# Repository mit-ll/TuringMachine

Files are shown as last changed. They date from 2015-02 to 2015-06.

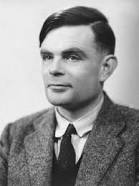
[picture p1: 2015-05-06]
student_code/Trevon/turing.jpg

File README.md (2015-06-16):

# A Turing Machine by MIT Lincoln Laboratory and the Community Charter School of Cambridge

During the spring semester in 2015, a team of MIT Lincoln Laboratory (http://www.ll.mit.edu/) staff volunteered there time to build a Turing machine with two high school seniors from the Community Charter School of Cambridge (http://www.ccscambridge.org/). This project helped the two seniors satisfy their internship requirement. The Turing machine was conceptualized by Alan Turing in 1936, but has been implemented in a more modern form.  The design uses 35mm film as memory, on which bits are physically written, read, and erased with a marker, camera, and mechanical eraser respectively.  These mechanisms are used to control the evolution of a state machine; fulfilling Turing's requirements for arbitrary computation.  The machine is controlled by embedded micro controllers, numerous motors and sensors, and code that was developed with the students.  The entire design for the machine, as well as the manufacturing and assembly, was created throughout the internship. The technical team from Lincoln Laboratory consisted of Chad Spensky, Benjamin Nahill, Timothy Greer, Matthew Harger, Stuart Baker, and Jack Lepird.  

## Contents
This repository contains all of the models, code, and bill of materials used to create our turing machine.

## Resources
  - [A Turing Machine](http://aturingmachine.com/)
  - [Turing Machine Emulator](http://www.turing.org.uk/turing/scrapbook/tmjava.html)
  - [Dimensions of 35mm film](http://www.brianpritchard.com/Fig%202.jpg)
  - [Dimensions of 35mm film (alt)](https://www.stereoscopy.com/faq/standard35ansi.gif)
  - [Robotic Calligraphy](http://calligraphybyherald.wix.com/herald#!gallery/c1zy6)

### Parts
 - [35mm Film Leader](http://www.numbersfilmsupply.com/categories/FILM-SUPPLIES/LEADER/)

## Raspberry Pi
 - [Touchscreen Drivers] (http://engineering-diy.blogspot.com/2013/01/adding-7inch-display-with-touchscreen.html)
 - [Modifying the Pi SD card on a Mac](http://pi.gbaman.info/?p=328)

### Setting up the console cable
 - The following [tutorial](https://learn.adafruit.com/downloads/pdf/adafruits-raspberry-pi-lesson-5-using-a-console-cable.pdf) worked perfectly.  Screen should be able connect to the serial port after you install the driver.

 >screen /dev/tty.usbserial 115200

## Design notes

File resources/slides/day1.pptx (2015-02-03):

## Cambridge Charter School Internship Building a Turing Machine

Chad Spensky, Tim Greer, Jack Lepird, Stuart Baker
Feb 3 2015

## Who are we?

- Chad Spensky
  - Area of Expertise: Computer Security
  - Education:
    - Bachelor’s Degree
      - Mathematics / Comp Sci. / Econ. @ PITT
    - Master’s Degree
      - Computer Security @ UNC-CH
  - Research Interests:
    - Authentication, Low-level Malware Analysis, Embedded Systems
  - Hobbies:
    - Snowboarding, Volleyball, Basketball, Inner Tube Water Polo, Traveling, Tinkering

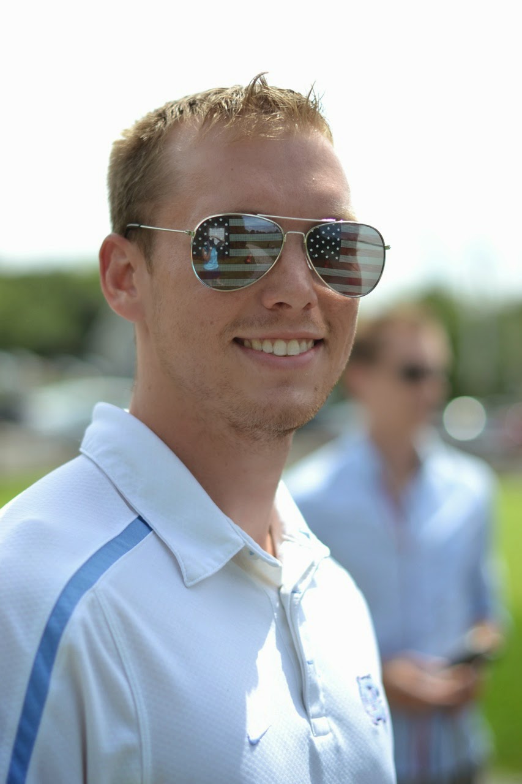
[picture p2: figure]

## Who are we?

- Jack Lepird
  - Areas of Expertise:
    - Machine Learning, Optimization, and Artificial Intelligence
  - Education:
    - Bachelor's Degree:
      - Mathematics / Operations Research / German, United States Air Force Academy
    - Master’s Degree (underway):
      - Operations Research, Massachusetts Institute of Technology
  - Research Interest:
    - Next-Generation Aircraft Collision Avoidance Systems
  - Hobbies:
    - Travel, SCUBA, Golf

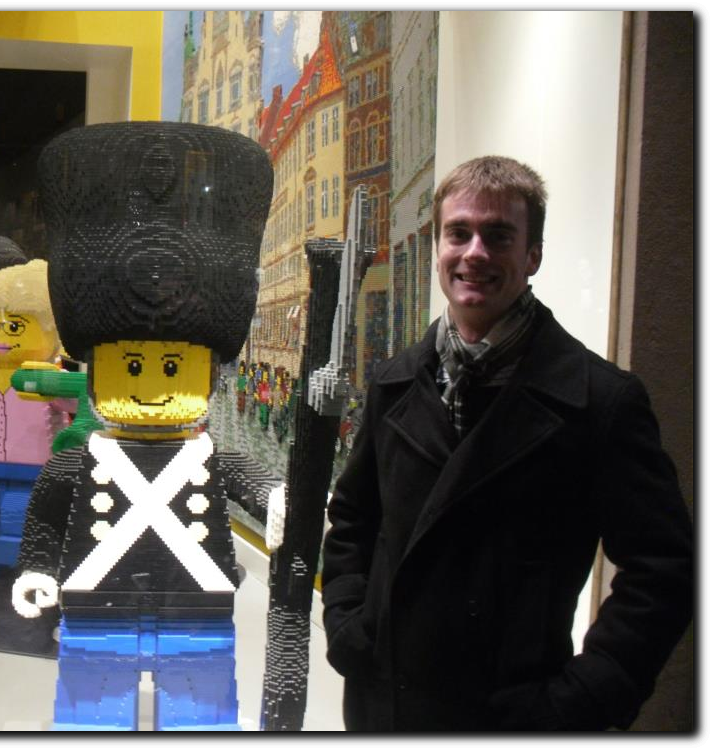
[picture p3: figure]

## Who are we?

- Tim Greer

## Who are we?

- Stuart Baker

## Who are you?

- What are your favorite subjects?
- What is your favorite food/color/animal?
- What do you do for fun?
- What do you hope to get out of this internship?

## Why are we here?

To Build a Turing Machine!

## Why are we here?

A WHAT?! Machine?

## Alan Turing

- One of the fathers of Computer Science
- Cracked German “Enigma” code during WWII
  - Shorted war by “two to four years”
- Solved “Entscheidungsproblem”
  - One of the “problems of the [20th] century”
- Could run marathon in under 2hrs 30 min
  - 5:45 minute miles
- Basically, a huge stud

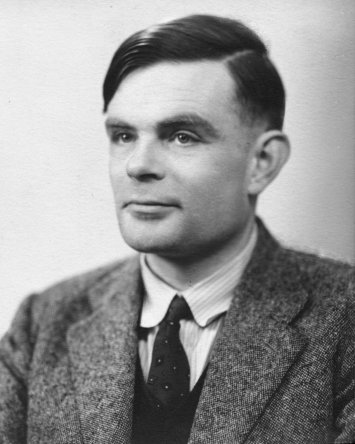
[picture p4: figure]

## What is a Turing Machine?

- A mental exercise
- Consists of three parts:
  - Tape
  - Head
  - “Machine State”
- Three operations:
  - Change symbol on tape
  - Move Tape
  - Change “state”

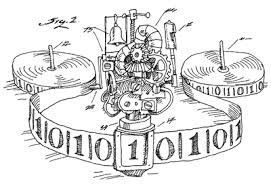
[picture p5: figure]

## So, why do we care?

- Anything computable can be run on a Turing Machine
  - Weird, right?
  - Weirder: In theory, the Turing machine is more powerful than your computer!
  - Studying a Turing machine can show us the limits of computing
- Provides a useful model for a Central Processing Unit (CPU) in an electronic computer

In fact, CPU instructions (right) look very similar to Turing Machine instructions

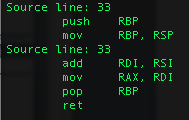
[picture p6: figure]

## Our semester goal

www.aturingmachine.com

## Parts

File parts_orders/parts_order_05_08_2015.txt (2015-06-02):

1 - 3ft of 6061 Aluminum (8mm Diameter) http://www.mcmaster.com/#standard-aluminum-rods/=x39eac
4 - Metric 18-8 Stainless Steel Unthreaded Spacer (4.5mm OD, 3mm Length, M3
Screw Size) http://www.mcmaster.com/#unthreaded-spacers/=x39gic

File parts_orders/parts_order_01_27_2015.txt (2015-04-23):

3 - Pi Starter Kits (https://www.adafruit.com/products/2125)
3 - Pi Cameras (https://www.adafruit.com/products/1367)
1 - Shift Registers (https://www.adafruit.com/products/450)
3 - Motor Kits (https://www.adafruit.com/products/1438)
3 - Motor Sheilds for Pi (https://www.adafruit.com/products/2348)
3 - Stepper Motors (https://www.adafruit.com/products/324)

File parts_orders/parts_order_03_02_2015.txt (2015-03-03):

1 - 35mm Film Leader/ Blue (http://www.ebay.com/itm/35MM-MOTION-PICTURE-FILM-LEADER-1000FT-ROLL-/351289908925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)
1 - Dry Erase Markers (http://www.amazon.com/Dry-Erase-Chalk-Marker-White/dp/B00L8BAXR0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)

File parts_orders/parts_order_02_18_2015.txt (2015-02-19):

2 - Power Supply for Monitor (http://www.amazon.com/Tontec%C2%AE-Supply-Adapter-Raspberry-Resolution/dp/B00LFBPL7K)
1 - Micro USB Cables (http://www.amazon.com/Anker-Premium-Android-Samsung-Motorola/dp/B00N8VHW72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)
5 - USB A to B (http://www.amazon.com/Belkin-3FT-USB-Device-Cable/dp/B00004Z5IU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)
1 - OpeanBeam (http://www.adafruit.com/products/1274)
3 - Motor Shields (http://www.adafruit.com/products/1438)
4 - Servos (http://www.adafruit.com/products/155)

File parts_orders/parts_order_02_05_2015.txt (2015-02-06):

2 - Touch Screen (http://www.amazon.com/Tontec-Raspberry-Display-AT070TN90-Touchscreen/dp/B00HNLXZHO)
3 - Raspberry Pi 2.0 (http://www.adafruit.com/products/2358)
3 - Multimeters (http://www.adafruit.com/products/2034)
3 - Keyboard/Mouse for Raspbery Pis (http://www.adafruit.com/products/1738)
2 - Film Leader/Our Tape (http://www.ebay.com/itm/Super-8mm-Film-Leader-50-ft-White-Leader-for-Super-8mm-/191495457883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)

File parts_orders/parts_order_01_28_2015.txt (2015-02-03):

3 - Pi Starter Kits (https://www.adafruit.com/products/2125)
3 - Pi Cameras (https://www.adafruit.com/products/1367)
1 - Shift Registers (https://www.adafruit.com/products/450)
3 - Motor Kits (https://www.adafruit.com/products/1438) [SOLD OUT]
3 - Motor Sheilds for Pi (https://www.adafruit.com/products/2348)
3 - Stepper Motors (https://www.adafruit.com/products/324)
3 - DC Motors (http://www.adafruit.com/products/711)
3 - Stepper Motors (http://www.adafruit.com/products/858)
3 - Solenoids (http://www.adafruit.com/products/412)
1 - Robotic Arm (http://www.adafruit.com/products/2012)
3 - Motor Kits (http://www.adafruit.com/products/1940)

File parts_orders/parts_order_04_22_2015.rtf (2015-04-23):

Things to Cut

Spools
4 - Laser cut spool holder sides
2 - Water jet base

Main Assembly
2 - Water jet base
1 - Main base
1 - Arm (top) for eraser
1 - Arm (bottom) for eraser
1 - Rail for marker arm (120mm)

Things to 3d Print

Spools
2 - Spool holder Hub
2 - Spool feeders with teeth for 35mm Film
2 - Spool timing pull (large)

Main Assembly
2 - Clamps for makers

Things to Buy

Overall
8mm Rod - http://www.banggood.com/OD-8mm-x-400mm-Bearing-Steel-Cylinder-Liner-Shaft-Optical-Axis-p-909003.html
2 Sheets of plastic (Black acrylic) - http://www.mcmaster.com/#8505k15/=wvbhm8

Spools
2 10K Potentiometer - https://www.adafruit.com/products/562
20 M3x10 tapered screws - http://www.metricscrews.us/index.php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
2 Stepper Brackets - https://solarbotics.com/product/52655/
2 Timing Pullys (Small) - https://sdp-si.com/eStore/Catalog/PartNumber/A%206Z%203-14DF03710
20 M3x30 Screws - hhttp://www.metricscrews.us/index.php?main_page=product_info&cPath=98_7_257&products_id=637 (https://www.etsy.com/listing/184820141/m3-x-30-mm-metric-machine-screws?kpid=184820141)

Main Assembly
1 Stepper Bracket - https://solarbotics.com/product/52655/
3 Servo Brackets - https://solarbotics.com/product/52650/
4 Bearing Mounts - https://solarbotics.com/product/52665/
3 Timing Pullys - https://sdp-si.com/eStore/Catalog/PartNumber/A%206Z%203-14DF03710

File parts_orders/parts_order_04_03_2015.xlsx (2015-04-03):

Part | Manufacturer | Manf # | Distributor | Dist # | Unit $ | Units | Total $ | Link
Aluminum plate, .125" Thick, 2 ft x 4 ft |  |  | McMaster Carr | 89015K28 | $50.58 | 1 | $50.58 | http://www.mcmaster.com/#89015k28/=wji07g
Multipurpose 6061 Aluminum Tube, 1 [ft] |  |  | McMaster Carr | 9056K74 | $9.18 | 1 | $9.18 | http://www.mcmaster.com/#9056k74/=wb0jrw
Architectural, 9/16" OD, 0.118" Wall, 2 [ft] |  |  | McMaster Carr | 1658T34 | $4.61 | 1 | $4.61 | http://www.mcmaster.com/#1658t34/=wjhpzd
Spacers, 6mm OD, 25mm Length, M3 |  |  | McMaster Carr | 94669A739 | $1.32 | 12 | $15.84 | http://www.mcmaster.com/#94669a739/=wde7l8
Clamp-on Shaft Collar, 8mm |  |  | McMaster Carr | 9506T4 | $4.14 | 4 | $16.56 | http://www.mcmaster.com/#9506t4/=wjhrlv
Aluminum Flat Washer, M8, 10 pack |  |  | McMaster Carr | 92334A116 | $10.22 | 1 | $10.22 | http://www.mcmaster.com/#92334a116/=wjhs23
Stepper Motor, NEMA 17 Frame |  | SM-42BYG011-25 | Sparfun | ROB-09238 | $14.95 | 3 | $44.85 | https://www.sparkfun.com/products/9238
Linear Stepper Motor |  | 39BYGL | Sparfun | ROB-10848 | $29.95 | 1 | $29.95 | https://www.sparkfun.com/products/10848
Low Profile Servo | Hitec | HS-77BB | Amazon | B0006O3WQY | $24.96 | 1 | $24.96 | http://www.amazon.com/Hitec-RCD-31077S-HS-77BB-Profile/dp/B0006O3WQY/
Shaft Support |  |  | Adafruit | 1182 | $3.95 | 4 | $15.80 | https://www.adafruit.com/products/1182
Aluminum Flex Shaft Coupler - 5mm to 8mm |  |  | Adafruit | 1176 | $4.95 | 3 | $14.85 | https://www.adafruit.com/products/1176
Radial Ball Bearing 608ZZ - Set of 4 |  |  | Adafruit | 1178 | $6.95 | 3 | $20.85 | https://www.adafruit.com/products/1252
Supported Slide Rail - 15mm wide - 500mm long |  |  | Adafruit | 1861 | $29.95 | 1 | $29.95 | https://www.adafruit.com/products/1861
15mm Slide Railing Platform - Smaller Size |  |  | Adafruit | 1860 | $21.95 | 1 | $21.95 | https://www.adafruit.com/products/1860
Timing Pulley, XL Pitch, 14 Teeth |  |  | SDP-SI | A 6Z 3-14DF03710 | $7.42 | 5 | $37.10 | https://sdp-si.com/eStore/Catalog/PartNumber/A%206Z%203-14DF03710
UV Leds |  |  | Adafruit | 1793 | $4.95 | 1 | $4.95 | http://www.adafruit.com/products/1793
Camera Ribbon Cable |  |  | Adafruit | 1731 | $2.95 | 1 | $2.95 | http://www.adafruit.com/products/1731
Dry Erase Makers (Neon) |  |  | Amazon | SAN1752226 | $6.70 | 1 | $6.70 | http://www.amazon.com/Expo-Bullet-Erase-Markers-Colored/dp/B0033AGVVG
Dry Erase Markers (Glow) |  |  | Amazon | 79551 | $8.99 | 1 | $8.99 | http://www.amazon.com/Quartet-Glo-write-Dry-Erase-Assorted-79551/dp/B008DQXN48
 |  |  |  |  |  | Total | $370.84

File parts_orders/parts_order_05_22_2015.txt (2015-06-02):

1 - http://www.mcmaster.com/#6484k231/=xa42p9
1 - http://www.mcmaster.com/#6484k23/=xa43nw
1 - http://www.mcmaster.com/#6484k232/=xa43of
2 - http://www.mcmaster.com/#6484K228

2 - http://www.mcmaster.com/#6484k227/=xalcii

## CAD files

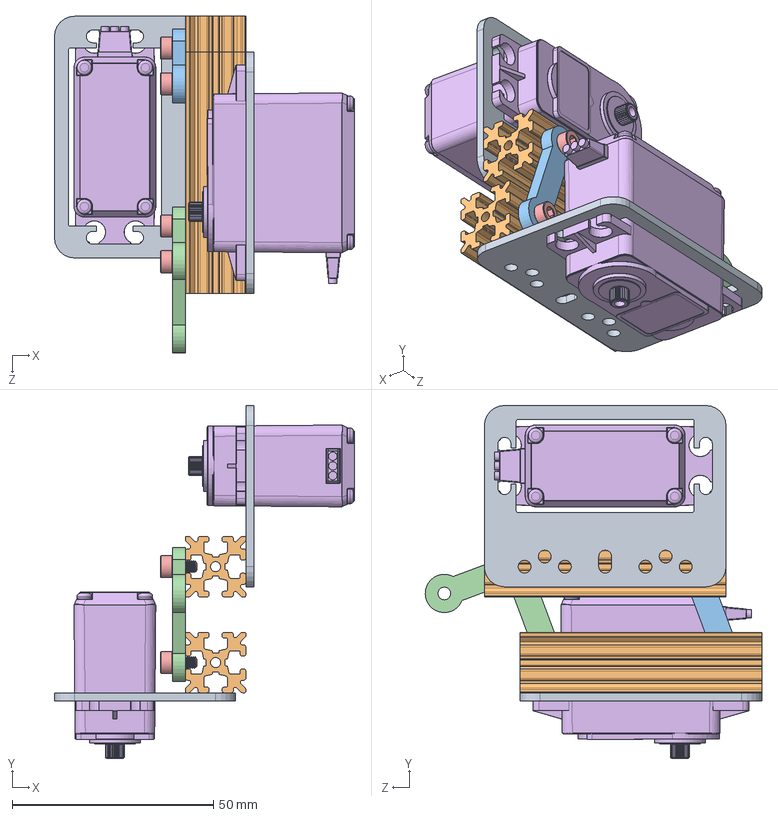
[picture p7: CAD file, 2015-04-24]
models/Gantry/Eraser/Assemembly_Eraser.SLDASM
74.5 x 87.6 x 83.5 mm
Plate_Servo_Mount x 2
Eraser_Beam_Riser x 2
Lift_Arm
Lift_Arm_Driven
Bolt_M3_6mm x 4
Servo x 2

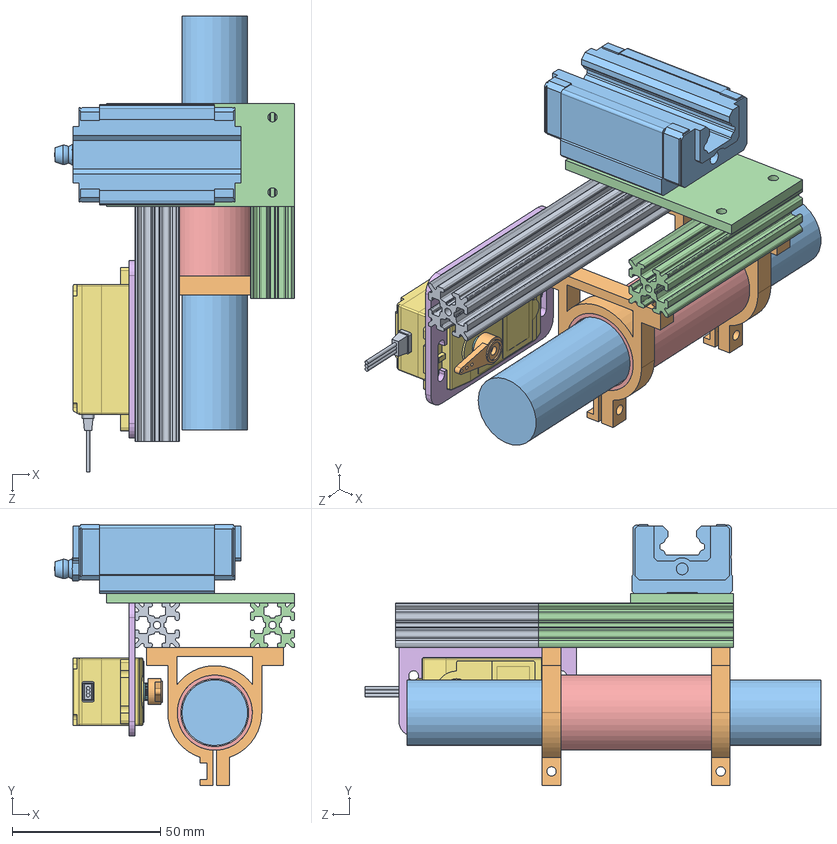
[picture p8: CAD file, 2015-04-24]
models/Gantry/Marker_Holder/Assembly_Marker_Holder.SLDASM
81.2 x 88.1 x 153.9 mm
Beam_Clamp_Riser
gantry_marker_clamp x 2
whiteboad_marker
Beam_Clamp_Riser_Short
Marker_Tube
Plate_Servo_Mount
Servo_SDS-S0070_Body
Servo_SDS-S0070_Shaft
Servo_SDS-S0070_Connector
Servo_SDS-S0070_Horn
Adafruit_Guide_Carriage
Carriage_Mounting_Plate

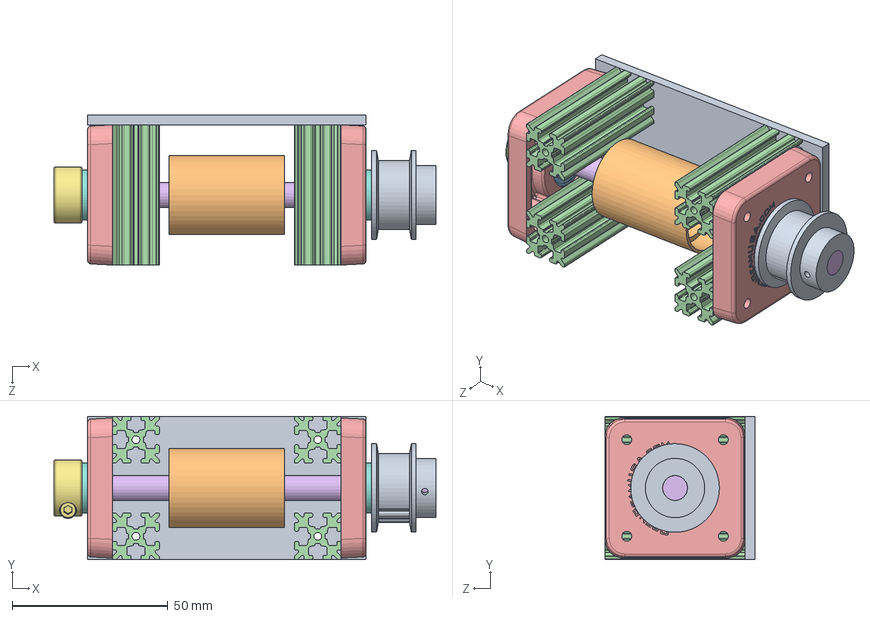
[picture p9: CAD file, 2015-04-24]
models/Gantry/Film_Feeder/Assembly_Film_Feeder.SLDASM
122.6 x 46.0 x 48.2 mm
Base_Plate
Film_Sprocket
Bearing_ID6mm_OD22mm x 2
Beam_Riser x 4
Plate_608_to_NEMA17 x 2
Feeder_Support_Rod
Shaft_Collar
Washer_M8 x 2
Timing_Pulley_14T

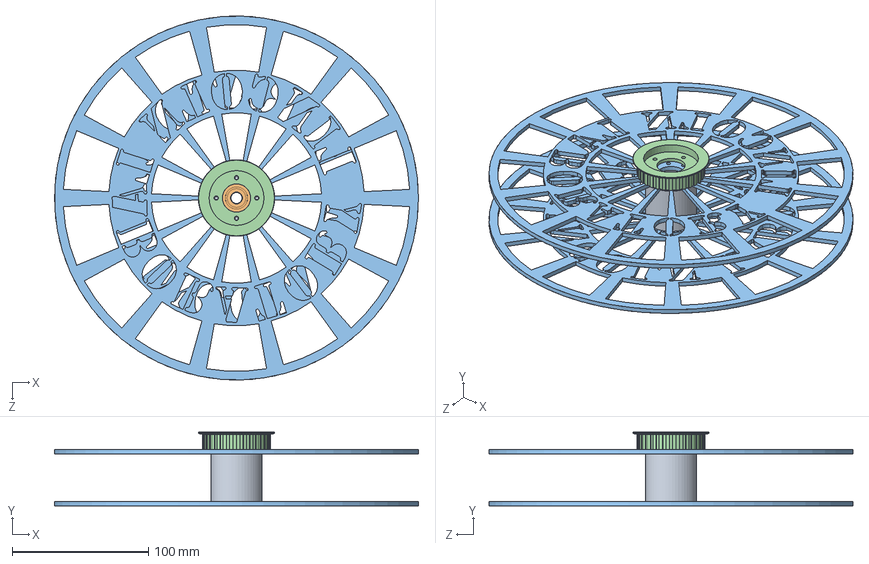
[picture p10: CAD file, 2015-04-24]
models/Spool_Holder/Spool/Assembly_Spool.SLDASM
266.7 x 54.1 x 266.6 mm
Spool_Hub
Bearing_ID6mm_OD22mm x 2
Spool_Side_Plate x 2
Timing_Pulley

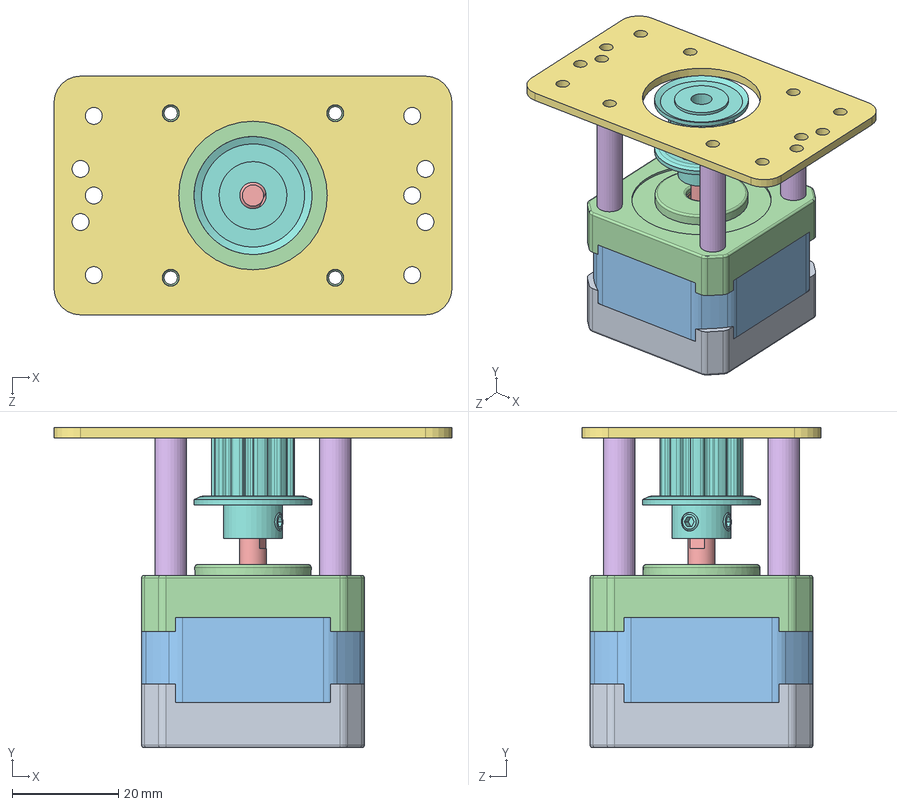
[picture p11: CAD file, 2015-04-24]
models/Gantry/Assembly_Film_Drive.SLDASM
75.0 x 60.4 x 45.0 mm
NEMA17_Bottom_33mm
radial ball bearing_68_din x 2
NEMA17_Middle_33mm
NEMA17_Top_33mm
NEMA17_Shaft_33mm
Motor_Spacer x 4
Plate_NEMA_17
Timing_Belt_Gear_11T

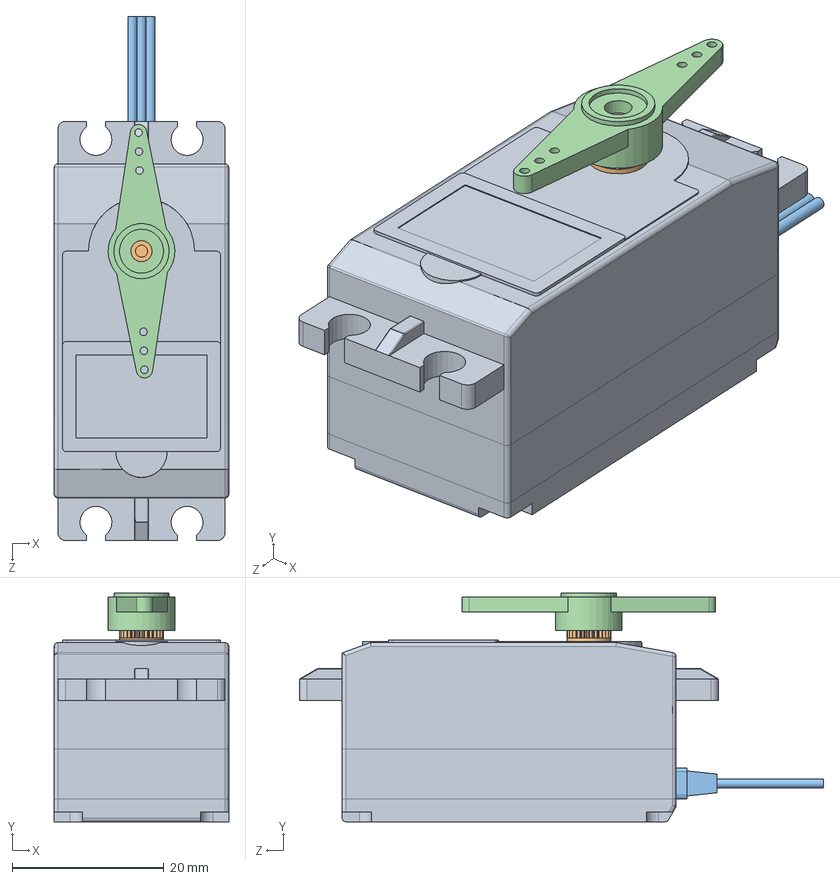
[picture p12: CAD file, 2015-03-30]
models/Gantry/Marker_Holder/Servo/Assembly_Servo_SDS-S0070.SLDASM
23.0 x 30.1 x 69.0 mm
Servo_SDS-S0070_Body
Servo_SDS-S0070_Shaft
Servo_SDS-S0070_Connector
Servo_SDS-S0070_Horn

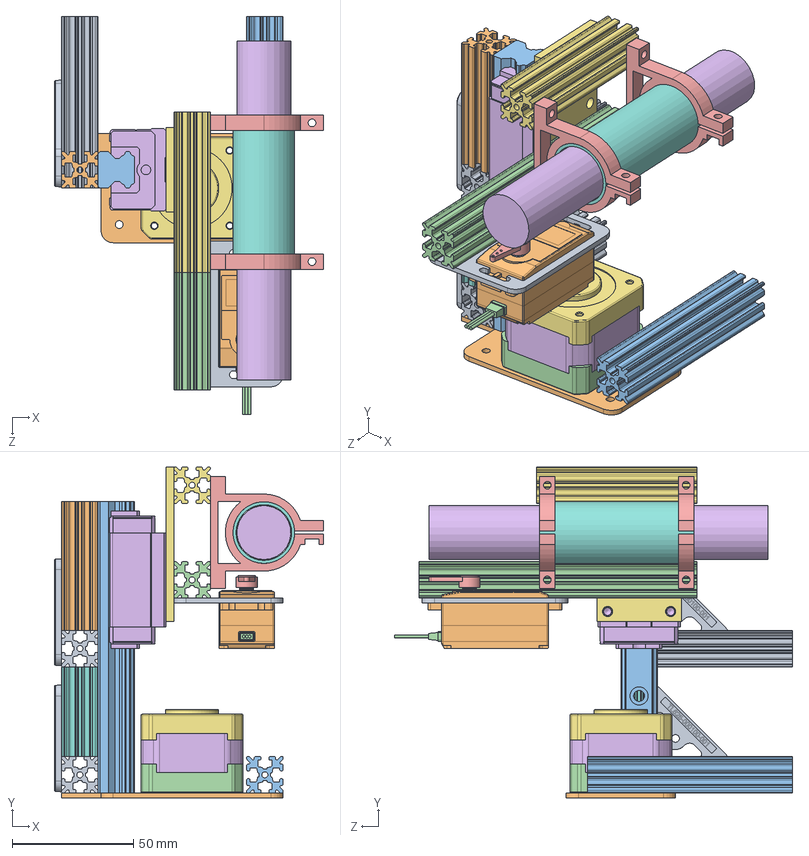
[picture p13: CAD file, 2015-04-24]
models/Gantry/Assembly_Gantry_Superstructure.SLDASM
110.8 x 136.3 x 163.9 mm
Beam_Gantry_Riser x 2
Beam_Gantry_Runner
Adafruit_Guide_Rail_Cut
Beam_Clamp_Riser
gantry_marker_clamp x 2
whiteboad_marker
Beam_Clamp_Riser_Short
Marker_Tube
Plate_Servo_Mount
Servo_SDS-S0070_Body
Servo_SDS-S0070_Shaft
Servo_SDS-S0070_Connector
Servo_SDS-S0070_Horn
Adafruit_Guide_Carriage
Carriage_Mounting_Plate
Beam_Gantry_Runner_Short
Plate_L x 2
Plate_NEMA_Modified
Beam_Gantry_Riser_Tall
NEMA17_Bottom_33mm
radial ball bearing_68_din x 2
NEMA17_Middle_33mm
NEMA17_Top_33mm

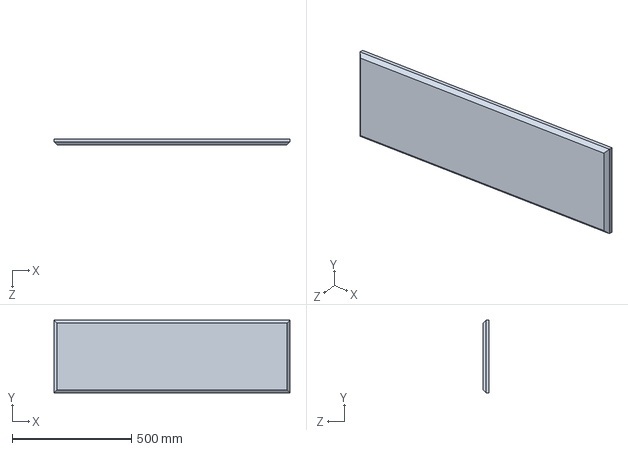
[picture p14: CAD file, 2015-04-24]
models/Display_Base.SLDPRT
990.6 x 304.8 x 25.4 mm

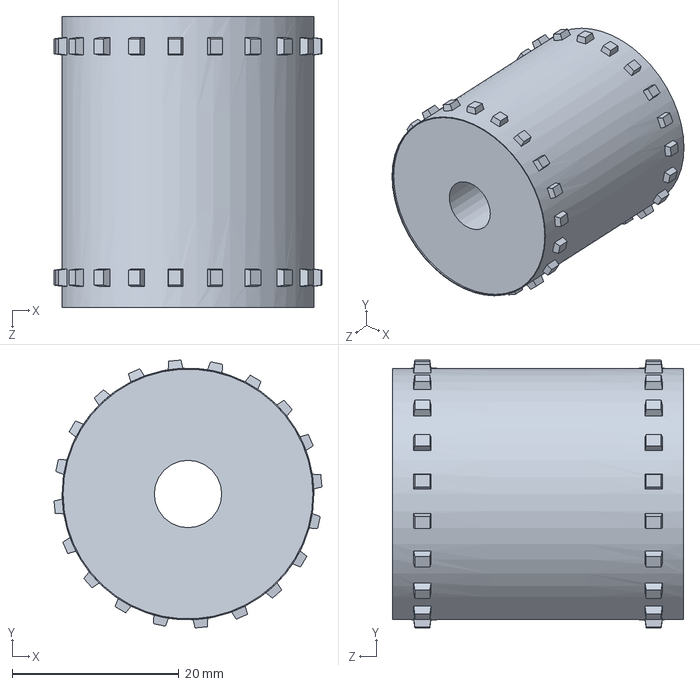
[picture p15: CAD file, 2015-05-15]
models/Gantry/Film_Feeder/Film_Sprocket.SLDPRT
32.2 x 32.2 x 35.0 mm

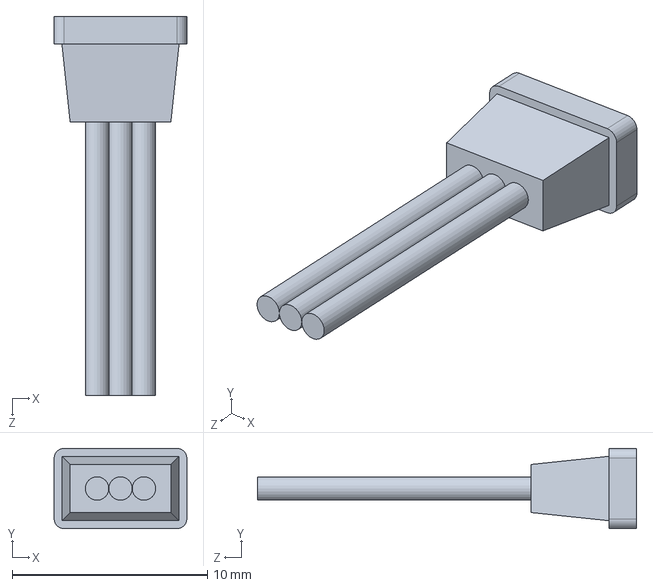
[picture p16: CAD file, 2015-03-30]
models/Gantry/Marker_Holder/Servo/Servo_SDS-S0070_Connector.SLDPRT
6.80 x 4.10 x 19.4 mm

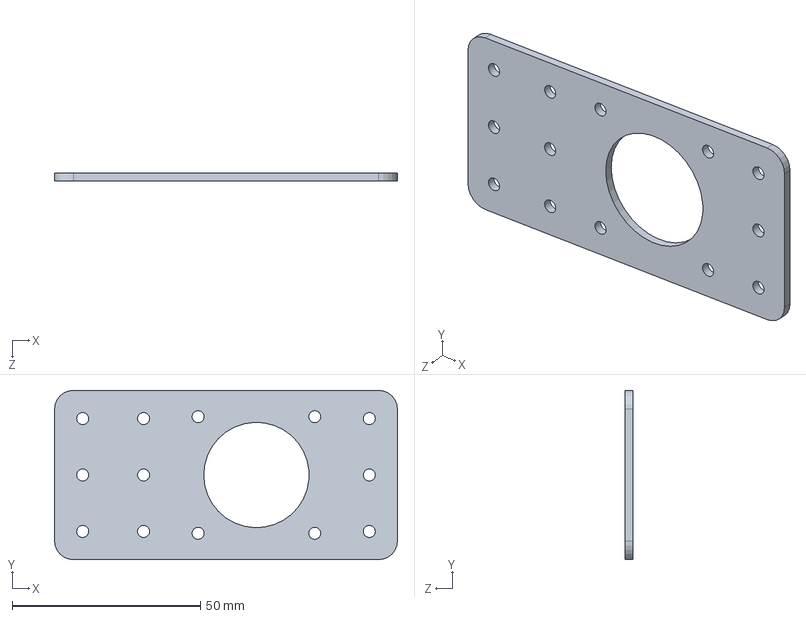
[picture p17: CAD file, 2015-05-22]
models/Gantry/Plate_NEMA_Modified2.SLDPRT
91.2 x 45.0 x 2.03 mm

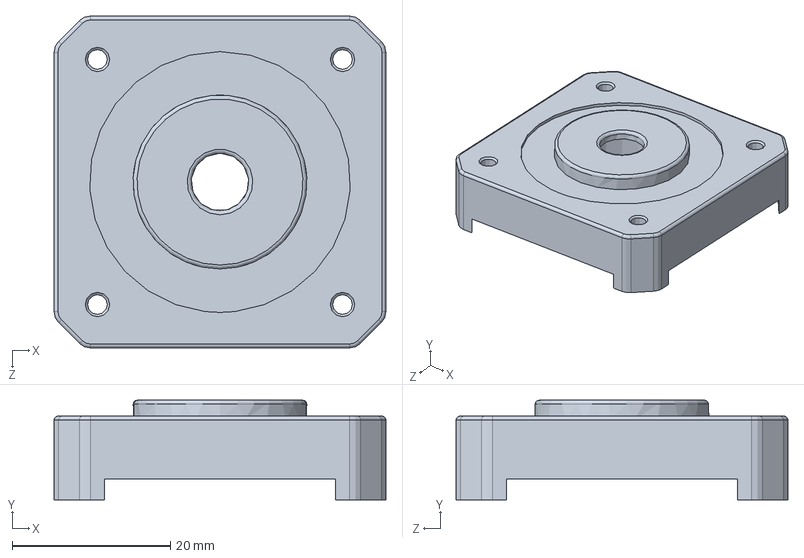
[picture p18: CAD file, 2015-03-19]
models/Nema-17_33mm/NEMA17_Top_33mm.SLDPRT
42.0 x 12.6 x 42.0 mm

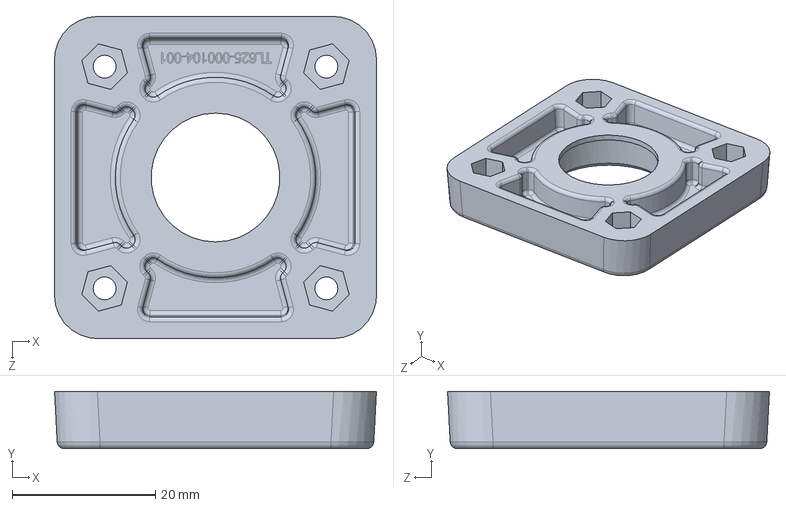
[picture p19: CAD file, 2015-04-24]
models/OpenBeam/Bearing_to_NEMA17/TL625-000104-001_-_608_to_NEMA_17_Adapter.SLDPRT
45.0 x 8.00 x 45.0 mm

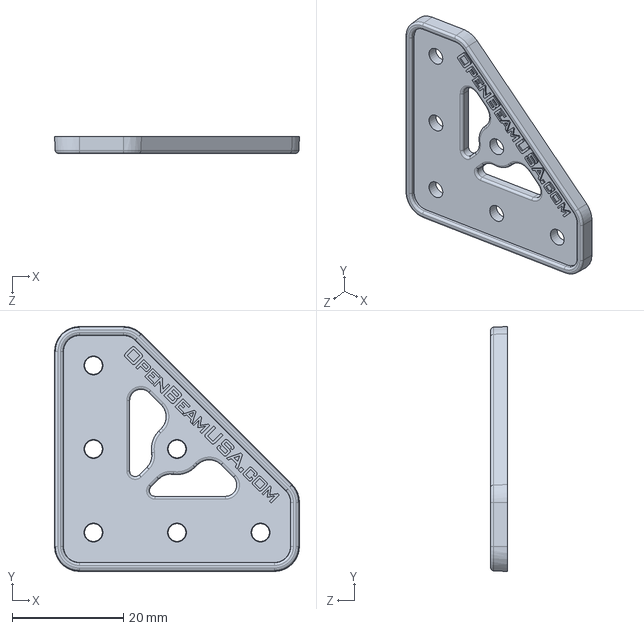
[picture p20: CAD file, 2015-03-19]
models/OpenBeam/L_Bracket/TL625-000100-002_-_L_Plate_OpenBeam_1515.SLDPRT
44.0 x 44.0 x 3.00 mm

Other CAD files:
models/OpenBeam/Motor_Mount_NEMA17/TL400-000105-002_-_NEMA_17_Motor_Mount.SLDPRT
models/OpenBeam/OpenBeam_Extrusion/TL-400-0101-002.SLDPRT
models/OpenBeam/Servo_Mount/TL400-000104-004_-_Plate_Servo_Mount_OpenBeam_1515.SLDPRT
models/OpenBeam/Shaft_Clamp/TL625-000102-001_-_SHAFT_CLAMP_OpenBeam_1515.SLDPRT
models/Adafruit_Guide_Carriage.SLDPRT
models/Adafruit_Guide_Rail.SLDPRT
models/Adafruit_Guide_Rail_Cut.SLDPRT
models/Adafruit_Rod_Support.SLDPRT
models/Angle_Connector.SLDPRT
models/Bearing_ID6mm_OD22mm.SLDPRT
models/Bolt_M3_10mm.SLDPRT
models/Bolt_M3_6mm.SLDPRT
models/Bolt_M3_8mm.SLDPRT
models/Coupler_8mm_5mm.SLDPRT
models/Gantry/Beam_Carraige_Riser.SLDPRT
models/Gantry/Beam_Carraige_Runner.SLDPRT
models/Gantry/Beam_Gantry_Riser.SLDPRT
models/Gantry/Beam_Gantry_Riser_Tall.SLDPRT
models/Gantry/Beam_Gantry_Runner.SLDPRT
models/Gantry/Beam_Gantry_Runner_Short.SLDPRT
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

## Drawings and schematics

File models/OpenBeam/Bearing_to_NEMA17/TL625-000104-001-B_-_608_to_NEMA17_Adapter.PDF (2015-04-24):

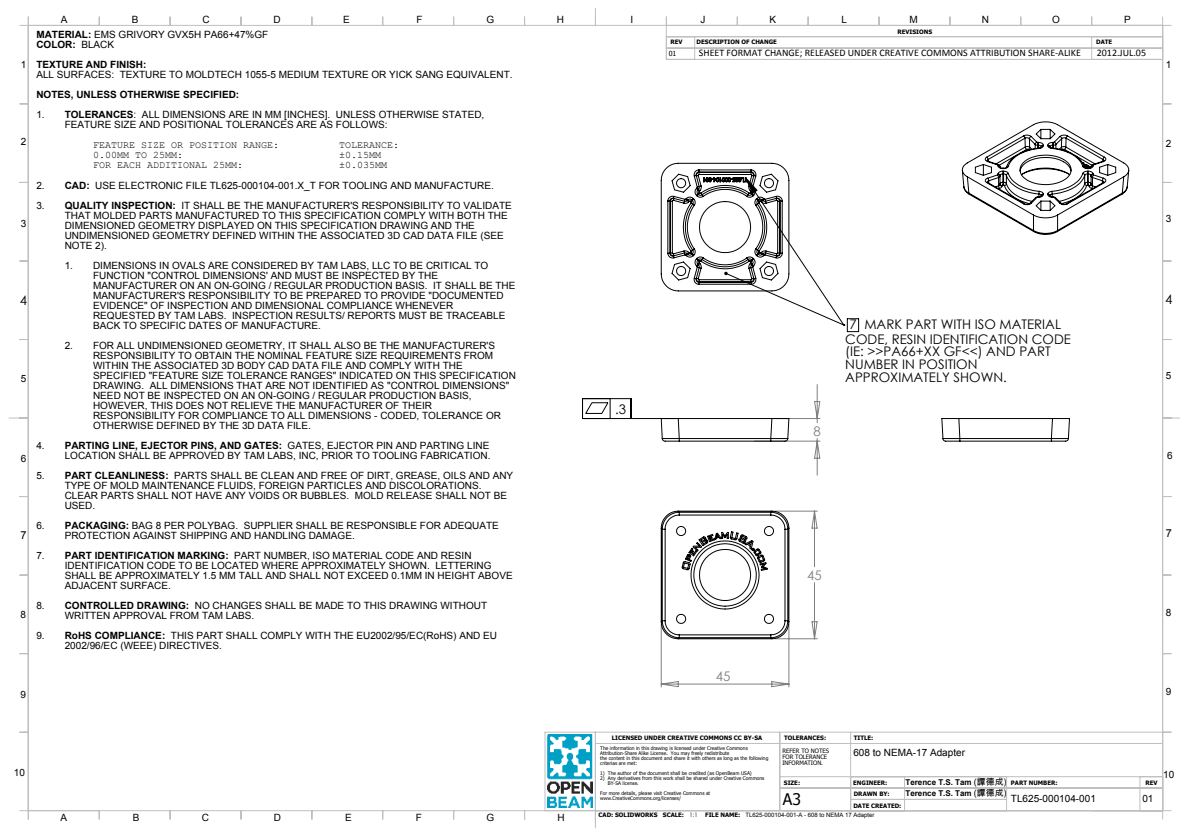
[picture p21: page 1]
FEATURE SIZE OR POSITION RANGE:; TOLERANCE:; FOR EACH ADDITIONAL 25MM:; CAD: SOLIDWORKS SCALE:; FILE NAME: 1:1; TL625-000104-001 DRAWN BY:; DATE CREATED:

MATERIAL: EMS GRIVORY GVX5H PA66+47%GF
COLOR: BLACK
TEXTURE AND FINISH:
ALL SURFACES: TEXTURE TO MOLDTECH 1055-5 MEDIUM TEXTURE OR YICK SANG EQUIVALENT.
NOTES, UNLESS OTHERWISE SPECIFIED:
1. TOLERANCES: ALL DIMENSIONS ARE IN MM [INCHES]. UNLESS OTHERWISE STATED,
FEATURE SIZE AND POSITIONAL TOLERANCES ARE AS FOLLOWS:

REV | DESCRIPTION OF CHANGE | DATE
01 | SHEET FORMAT CHANGE; RELEASED UNDER CREATIVE COMMONS ATTRIBUTION SHARE-ALIKE | 2012.JUL.05

2. CAD: USE ELECTRONIC FILE TL625-000104-001.X_T FOR TOOLING AND MANUFACTURE.
3. QUALITY INSPECTION: IT SHALL BE THE MANUFACTURER'S RESPONSIBILITY TO VALIDATE
THAT MOLDED PARTS MANUFACTURED TO THIS SPECIFICATION COMPLY WITH BOTH THE
DIMENSIONED GEOMETRY DISPLAYED ON THIS SPECIFICATION DRAWING AND THE
UNDIMENSIONED GEOMETRY DEFINED WITHIN THE ASSOCIATED 3D CAD DATA FILE (SEE
NOTE 2).
1. DIMENSIONS IN OVALS ARE CONSIDERED BY TAM LABS, LLC TO BE CRITICAL TO
FUNCTION "CONTROL DIMENSIONS' AND MUST BE INSPECTED BY THE
MANUFACTURER ON AN ON-GOING / REGULAR PRODUCTION BASIS. IT SHALL BE THE
MANUFACTURER'S RESPONSIBILITY TO BE PREPARED TO PROVIDE "DOCUMENTED
EVIDENCE" OF INSPECTION AND DIMENSIONAL COMPLIANCE WHENEVER
REQUESTED BY TAM LABS. INSPECTION RESULTS/ REPORTS MUST BE TRACEABLE
BACK TO SPECIFIC DATES OF MANUFACTURE.
2. FOR ALL UNDIMENSIONED GEOMETRY, IT SHALL ALSO BE THE MANUFACTURER'S
RESPONSIBILITY TO OBTAIN THE NOMINAL FEATURE SIZE REQUIREMENTS FROM
WITHIN THE ASSOCIATED 3D BODY CAD DATA FILE AND COMPLY WITH THE
SPECIFIED "FEATURE SIZE TOLERANCE RANGES" INDICATED ON THIS SPECIFICATION
DRAWING. ALL DIMENSIONS THAT ARE NOT IDENTIFIED AS "CONTROL DIMENSIONS"
NEED NOT BE INSPECTED ON AN ON-GOING / REGULAR PRODUCTION BASIS,
HOWEVER, THIS DOES NOT RELIEVE THE MANUFACTURER OF THEIR
RESPONSIBILITY FOR COMPLIANCE TO ALL DIMENSIONS - CODED, TOLERANCE OR
OTHERWISE DEFINED BY THE 3D DATA FILE.

7 MARK PART WITH ISO MATERIAL
CODE, RESIN IDENTIFICATION CODE
(IE: >>PA66+XX GF<<) AND PART
NUMBER IN POSITION
APPROXIMATELY SHOWN.

4. PARTING LINE, EJECTOR PINS, AND GATES: GATES, EJECTOR PIN AND PARTING LINE
LOCATION SHALL BE APPROVED BY TAM LABS, INC, PRIOR TO TOOLING FABRICATION.
5. PART CLEANLINESS: PARTS SHALL BE CLEAN AND FREE OF DIRT, GREASE, OILS AND ANY
TYPE OF MOLD MAINTENANCE FLUIDS, FOREIGN PARTICLES AND DISCOLORATIONS.
CLEAR PARTS SHALL NOT HAVE ANY VOIDS OR BUBBLES. MOLD RELEASE SHALL NOT BE
USED.
6. PACKAGING: BAG 8 PER POLYBAG. SUPPLIER SHALL BE RESPONSIBLE FOR ADEQUATE
7. PART IDENTIFICATION MARKING: PART NUMBER, ISO MATERIAL CODE AND RESIN
IDENTIFICATION CODE TO BE LOCATED WHERE APPROXIMATELY SHOWN. LETTERING
SHALL BE APPROXIMATELY 1.5 MM TALL AND SHALL NOT EXCEED 0.1MM IN HEIGHT ABOVE
ADJACENT SURFACE.
8. CONTROLLED DRAWING: NO CHANGES SHALL BE MADE TO THIS DRAWING WITHOUT
9. RoHS COMPLIANCE: THIS PART SHALL COMPLY WITH THE EU2002/95/EC(RoHS) AND EU
2002/96/EC (WEEE) DIRECTIVES.

PROTECTION AGAINST SHIPPING AND HANDLING DAMAGE.

WRITTEN APPROVAL FROM TAM LABS.

LICENSED UNDER CREATIVE COMMONS CC BY-SA

The information in this drawing is licensed under Creative Commons
Attribution-Share Alike License. You may freely redistribute
the content in this document and share it with others as long as the following
criterias are met:
1) The author of the document shall be credited (as OpenBeam USA)
2) Any derivatives from this work shall be shared under Creative Commons
BY-SA license.
For more details, please visit Creative Commons at
www.CreativeCommons.org/licenses/

REFER TO NOTES FOR TOLERANCE INFORMATION. | 608 to NEMA-17 Adapter

SIZE: | ENGINEER: | Terence T.S. Tam (譚德成) | PART NUMBER: | REV

Terence T.S. Tam (譚德成)

TL625-000104-001-A - 608 to NEMA 17 Adapter

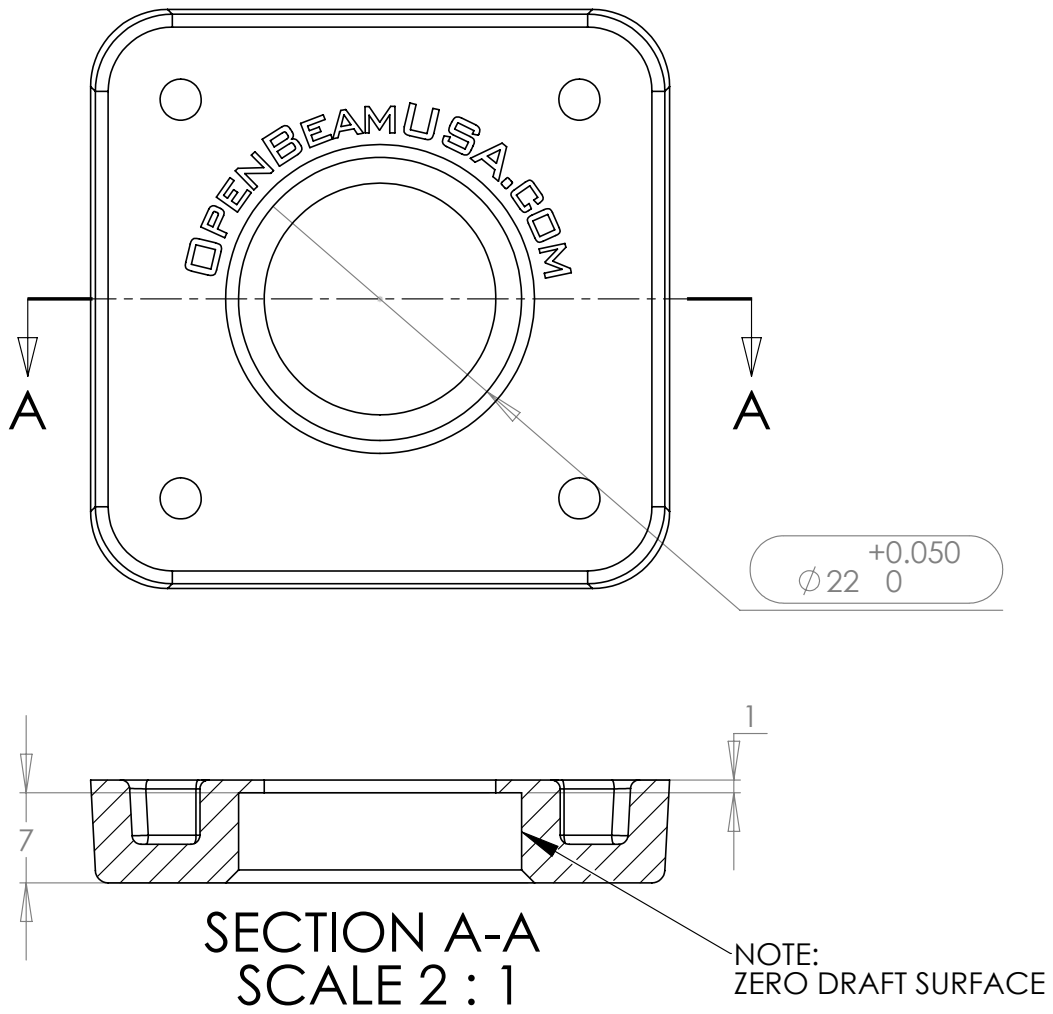
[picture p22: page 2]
SECTION A-A; SCALE 2 : 1; NOTE:; CAD: SOLIDWORKS SCALE:; FILE NAME: 1:1; TL625-000104-001 DRAWN BY:; DATE CREATED:

SEE REVISION BLOCK ON PAGE 1

ZERO DRAFT SURFACE

LICENSED UNDER CREATIVE COMMONS CC BY-SA

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

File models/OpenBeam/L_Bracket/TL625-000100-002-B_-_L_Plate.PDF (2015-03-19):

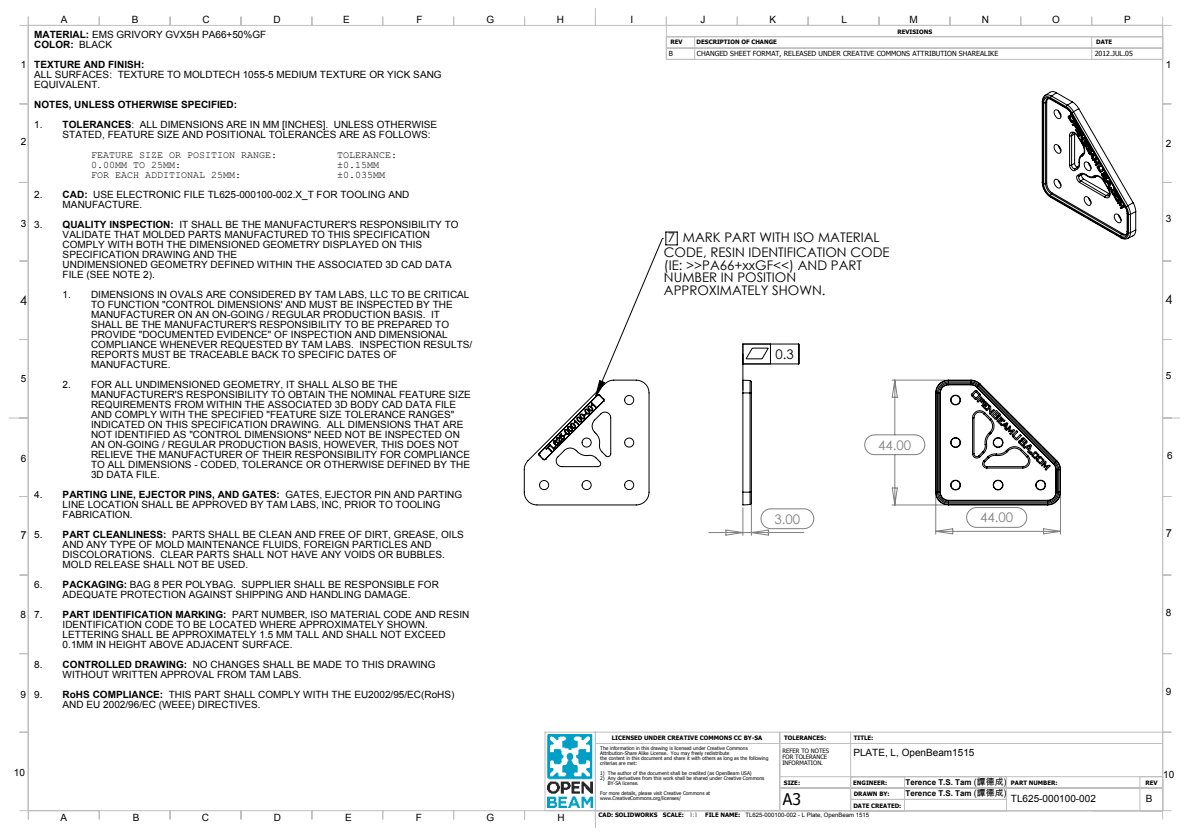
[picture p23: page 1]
FEATURE SIZE OR POSITION RANGE:; TOLERANCE:; FOR EACH ADDITIONAL 25MM:; CAD: SOLIDWORKS SCALE:; FILE NAME: 1:1; TL625-000100-002 DRAWN BY:; DATE CREATED: TL625-000100-002 - L Plate, OpenBeam 1515

MATERIAL: EMS GRIVORY GVX5H PA66+50%GF
COLOR: BLACK
TEXTURE AND FINISH:
ALL SURFACES: TEXTURE TO MOLDTECH 1055-5 MEDIUM TEXTURE OR YICK SANG
EQUIVALENT.
NOTES, UNLESS OTHERWISE SPECIFIED:
1. TOLERANCES: ALL DIMENSIONS ARE IN MM [INCHES]. UNLESS OTHERWISE
STATED, FEATURE SIZE AND POSITIONAL TOLERANCES ARE AS FOLLOWS:

REV | DESCRIPTION OF CHANGE | DATE
B | CHANGED SHEET FORMAT, RELEASED UNDER CREATIVE COMMONS ATTRIBUTION SHAREALIKE | 2012.JUL.05

2. CAD: USE ELECTRONIC FILE TL625-000100-002.X_T FOR TOOLING AND
MANUFACTURE.
3. QUALITY INSPECTION: IT SHALL BE THE MANUFACTURER'S RESPONSIBILITY TO
VALIDATE THAT MOLDED PARTS MANUFACTURED TO THIS SPECIFICATION
COMPLY WITH BOTH THE DIMENSIONED GEOMETRY DISPLAYED ON THIS
SPECIFICATION DRAWING AND THE
UNDIMENSIONED GEOMETRY DEFINED WITHIN THE ASSOCIATED 3D CAD DATA
FILE (SEE NOTE 2).
1. DIMENSIONS IN OVALS ARE CONSIDERED BY TAM LABS, LLC TO BE CRITICAL

7 MARK PART WITH ISO MATERIAL
CODE, RESIN IDENTIFICATION CODE
(IE: >>PA66+xxGF<<) AND PART
NUMBER IN POSITION
APPROXIMATELY SHOWN.

TO FUNCTION "CONTROL DIMENSIONS' AND MUST BE INSPECTED BY THE
MANUFACTURER ON AN ON-GOING / REGULAR PRODUCTION BASIS. IT
SHALL BE THE MANUFACTURER'S RESPONSIBILITY TO BE PREPARED TO
PROVIDE "DOCUMENTED EVIDENCE" OF INSPECTION AND DIMENSIONAL
COMPLIANCE WHENEVER REQUESTED BY TAM LABS. INSPECTION RESULTS/
REPORTS MUST BE TRACEABLE BACK TO SPECIFIC DATES OF
2. FOR ALL UNDIMENSIONED GEOMETRY, IT SHALL ALSO BE THE
MANUFACTURER'S RESPONSIBILITY TO OBTAIN THE NOMINAL FEATURE SIZE
REQUIREMENTS FROM WITHIN THE ASSOCIATED 3D BODY CAD DATA FILE
AND COMPLY WITH THE SPECIFIED "FEATURE SIZE TOLERANCE RANGES"
INDICATED ON THIS SPECIFICATION DRAWING. ALL DIMENSIONS THAT ARE
NOT IDENTIFIED AS "CONTROL DIMENSIONS" NEED NOT BE INSPECTED ON
AN ON-GOING / REGULAR PRODUCTION BASIS, HOWEVER, THIS DOES NOT
RELIEVE THE MANUFACTURER OF THEIR RESPONSIBILITY FOR COMPLIANCE
TO ALL DIMENSIONS - CODED, TOLERANCE OR OTHERWISE DEFINED BY THE
3D DATA FILE.

4. PARTING LINE, EJECTOR PINS, AND GATES: GATES, EJECTOR PIN AND PARTING
LINE LOCATION SHALL BE APPROVED BY TAM LABS, INC, PRIOR TO TOOLING
FABRICATION.
5. PART CLEANLINESS: PARTS SHALL BE CLEAN AND FREE OF DIRT, GREASE, OILS
AND ANY TYPE OF MOLD MAINTENANCE FLUIDS, FOREIGN PARTICLES AND
DISCOLORATIONS. CLEAR PARTS SHALL NOT HAVE ANY VOIDS OR BUBBLES.
MOLD RELEASE SHALL NOT BE USED.
6. PACKAGING: BAG 8 PER POLYBAG. SUPPLIER SHALL BE RESPONSIBLE FOR
ADEQUATE PROTECTION AGAINST SHIPPING AND HANDLING DAMAGE.
7. PART IDENTIFICATION MARKING: PART NUMBER, ISO MATERIAL CODE AND RESIN
IDENTIFICATION CODE TO BE LOCATED WHERE APPROXIMATELY SHOWN.
LETTERING SHALL BE APPROXIMATELY 1.5 MM TALL AND SHALL NOT EXCEED
0.1MM IN HEIGHT ABOVE ADJACENT SURFACE.
8. CONTROLLED DRAWING: NO CHANGES SHALL BE MADE TO THIS DRAWING
WITHOUT WRITTEN APPROVAL FROM TAM LABS.
9. RoHS COMPLIANCE: THIS PART SHALL COMPLY WITH THE EU2002/95/EC(RoHS)
AND EU 2002/96/EC (WEEE) DIRECTIVES.

LICENSED UNDER CREATIVE COMMONS CC BY-SA

The information in this drawing is licensed under Creative Commons
Attribution-Share Alike License. You may freely redistribute
the content in this document and share it with others as long as the following
criterias are met:
1) The author of the document shall be credited (as OpenBeam USA)
2) Any derivatives from this work shall be shared under Creative Commons
BY-SA license.
For more details, please visit Creative Commons at
www.CreativeCommons.org/licenses/

REFER TO NOTES FOR TOLERANCE INFORMATION. | PLATE, L, OpenBeam1515

SIZE: | ENGINEER: | Terence T.S. Tam (譚德成) | PART NUMBER: | REV

Terence T.S. Tam (譚德成)

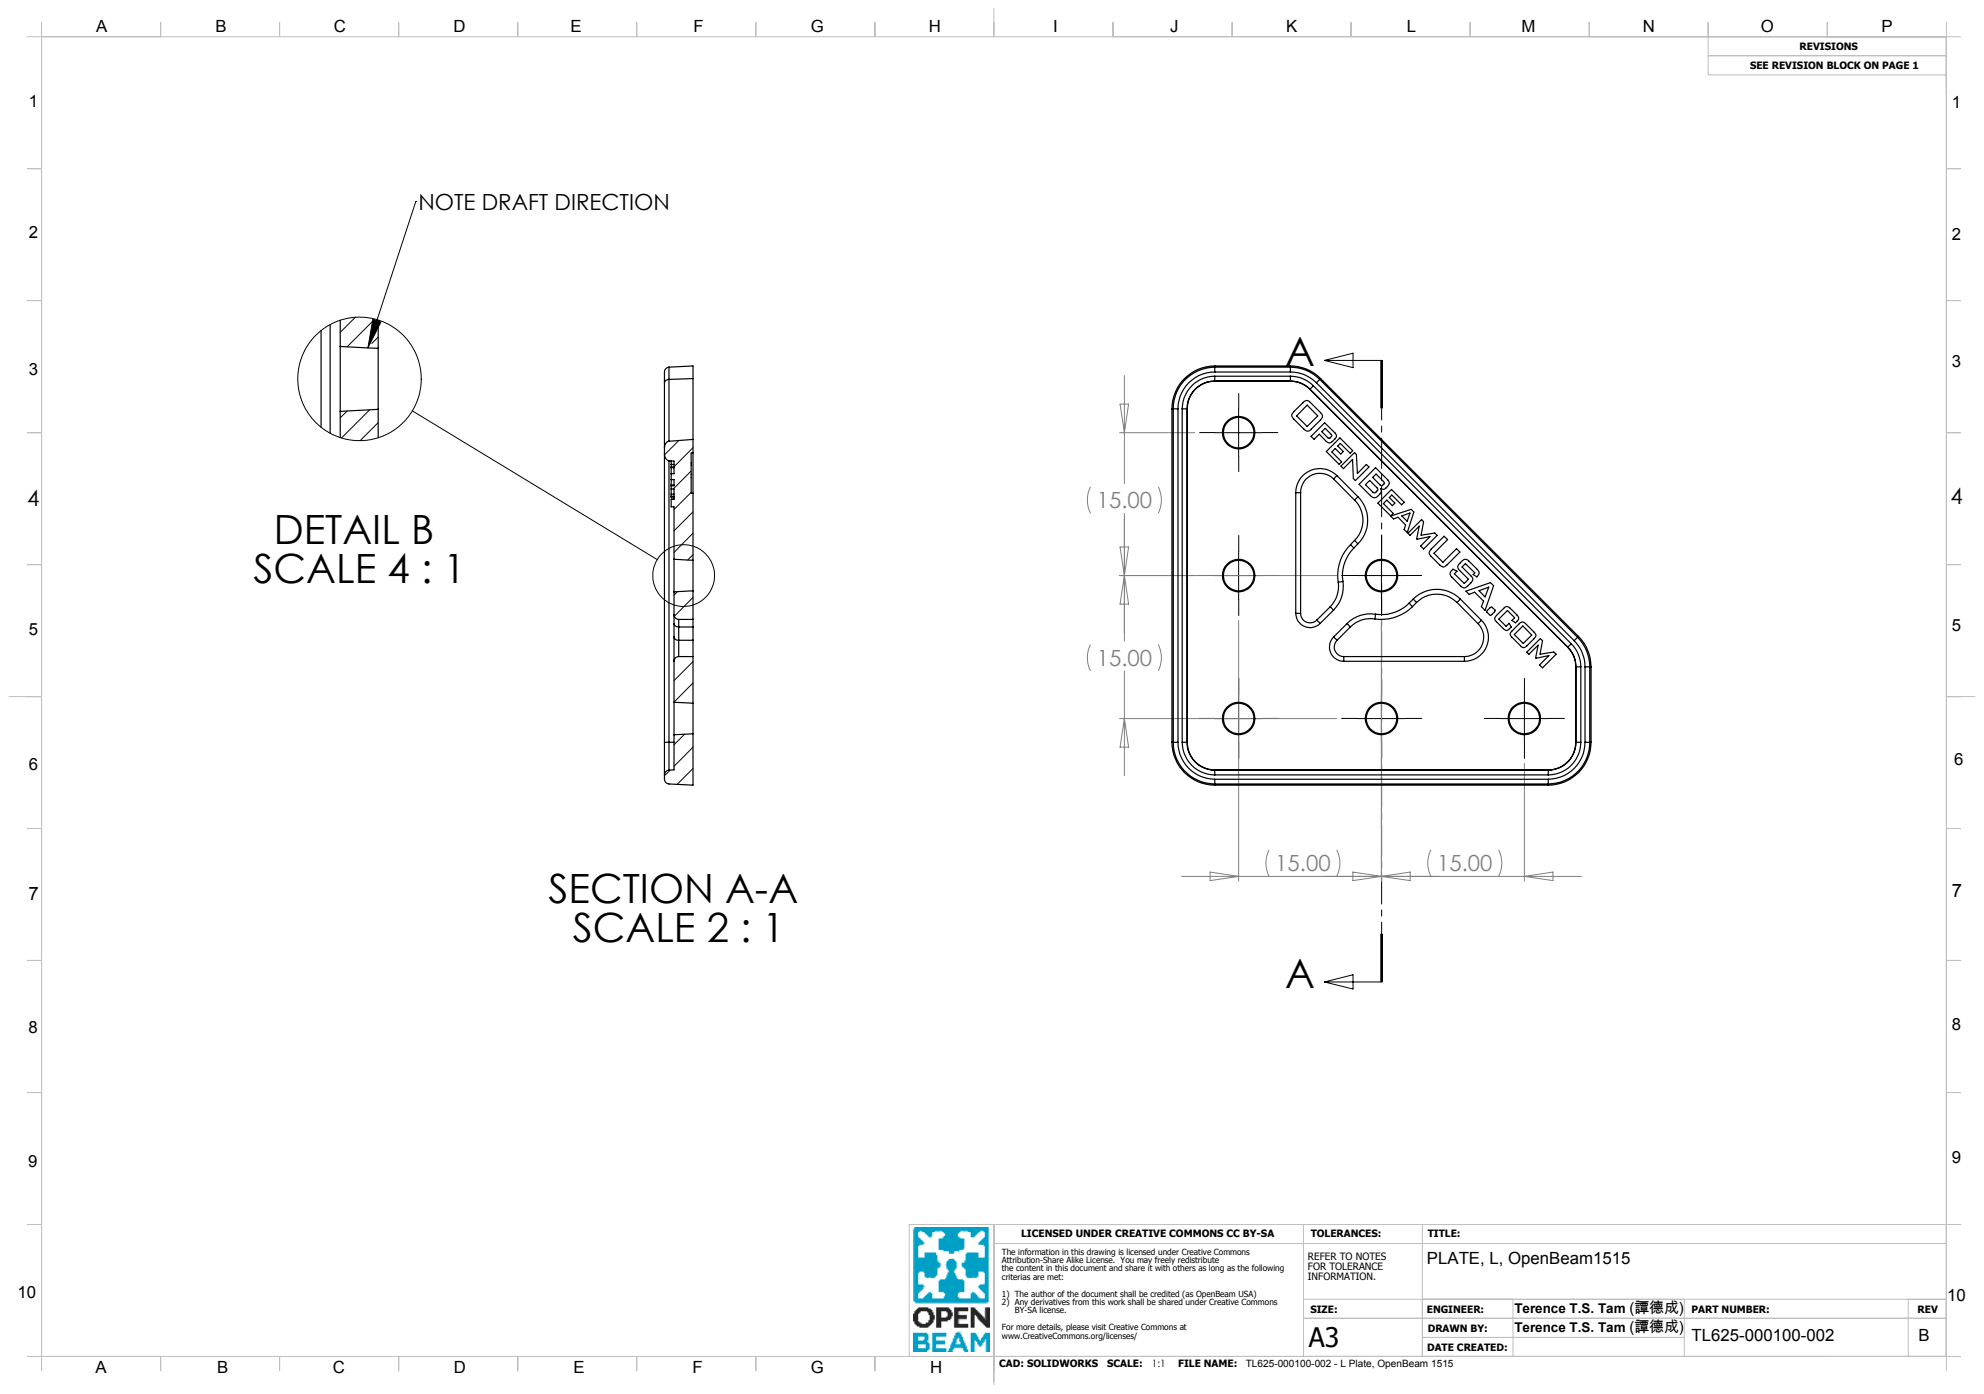
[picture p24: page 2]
SECTION A-A SCALE 2 : 1; DETAIL B SCALE 4 : 1; CAD: SOLIDWORKS SCALE:; FILE NAME: 1:1; TL625-000100-002 DRAWN BY:; DATE CREATED: TL625-000100-002 - L Plate, OpenBeam 1515

SEE REVISION BLOCK ON PAGE 1

NOTE DRAFT DIRECTION

LICENSED UNDER CREATIVE COMMONS CC BY-SA

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

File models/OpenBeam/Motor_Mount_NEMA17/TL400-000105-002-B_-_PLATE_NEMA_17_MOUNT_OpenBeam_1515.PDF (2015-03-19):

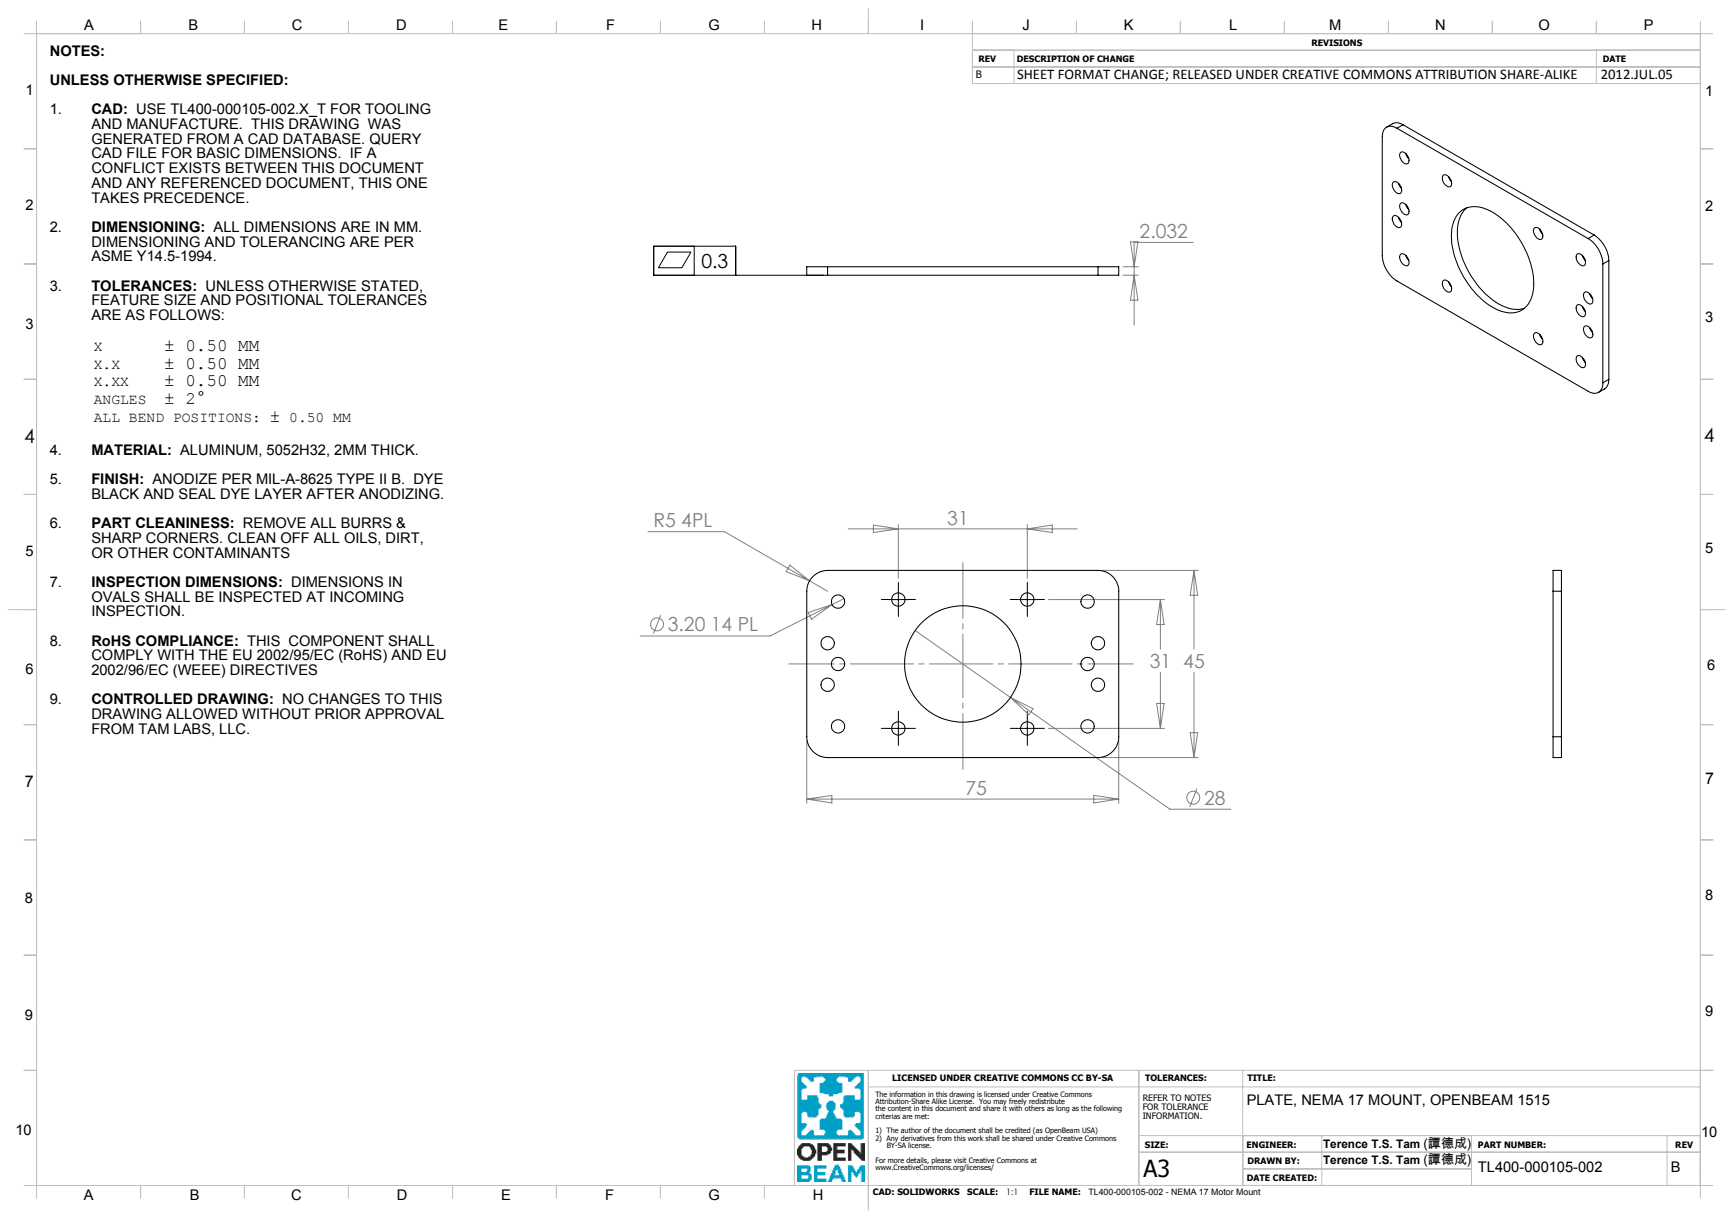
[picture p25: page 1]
CAD: SOLIDWORKS SCALE:; FILE NAME: 1:1; TL400-000105-002 DRAWN BY:; DATE CREATED:

NOTES:
UNLESS OTHERWISE SPECIFIED:
1. CAD: USE TL400-000105-002.X_T FOR TOOLING
AND MANUFACTURE. THIS DRAWING WAS
GENERATED FROM A CAD DATABASE. QUERY
CAD FILE FOR BASIC DIMENSIONS. IF A
CONFLICT EXISTS BETWEEN THIS DOCUMENT
AND ANY REFERENCED DOCUMENT, THIS ONE
TAKES PRECEDENCE.
2. DIMENSIONING: ALL DIMENSIONS ARE IN MM.
DIMENSIONING AND TOLERANCING ARE PER
ASME Y14.5-1994.
3. TOLERANCES: UNLESS OTHERWISE STATED,
FEATURE SIZE AND POSITIONAL TOLERANCES
ARE AS FOLLOWS:
ANGLES ± 2°
ALL BEND POSITIONS: ± 0.50 MM
4. MATERIAL: ALUMINUM, 5052H32, 2MM THICK.
5. FINISH: ANODIZE PER MIL-A-8625 TYPE II B. DYE
BLACK AND SEAL DYE LAYER AFTER ANODIZING.
6. PART CLEANINESS: REMOVE ALL BURRS &
SHARP CORNERS. CLEAN OFF ALL OILS, DIRT,
OR OTHER CONTAMINANTS
7. INSPECTION DIMENSIONS: DIMENSIONS IN
OVALS SHALL BE INSPECTED AT INCOMING
INSPECTION.
8. RoHS COMPLIANCE: THIS COMPONENT SHALL
COMPLY WITH THE EU 2002/95/EC (RoHS) AND EU
2002/96/EC (WEEE) DIRECTIVES
9. CONTROLLED DRAWING: NO CHANGES TO THIS
DRAWING ALLOWED WITHOUT PRIOR APPROVAL
FROM TAM LABS, LLC.

REV | DESCRIPTION OF CHANGE | DATE
B | SHEET FORMAT CHANGE; RELEASED UNDER CREATIVE COMMONS ATTRIBUTION SHARE-ALIKE | 2012.JUL.05

LICENSED UNDER CREATIVE COMMONS CC BY-SA

The information in this drawing is licensed under Creative Commons
Attribution-Share Alike License. You may freely redistribute
the content in this document and share it with others as long as the following
criterias are met:
1) The author of the document shall be credited (as OpenBeam USA)
2) Any derivatives from this work shall be shared under Creative Commons
BY-SA license.
For more details, please visit Creative Commons at
www.CreativeCommons.org/licenses/

REFER TO NOTES FOR TOLERANCE INFORMATION. | PLATE, NEMA 17 MOUNT, OPENBEAM 1515

SIZE: | ENGINEER: | Terence T.S. Tam (譚德成) | PART NUMBER: | REV

Terence T.S. Tam (譚德成)

TL400-000105-002 - NEMA 17 Motor Mount

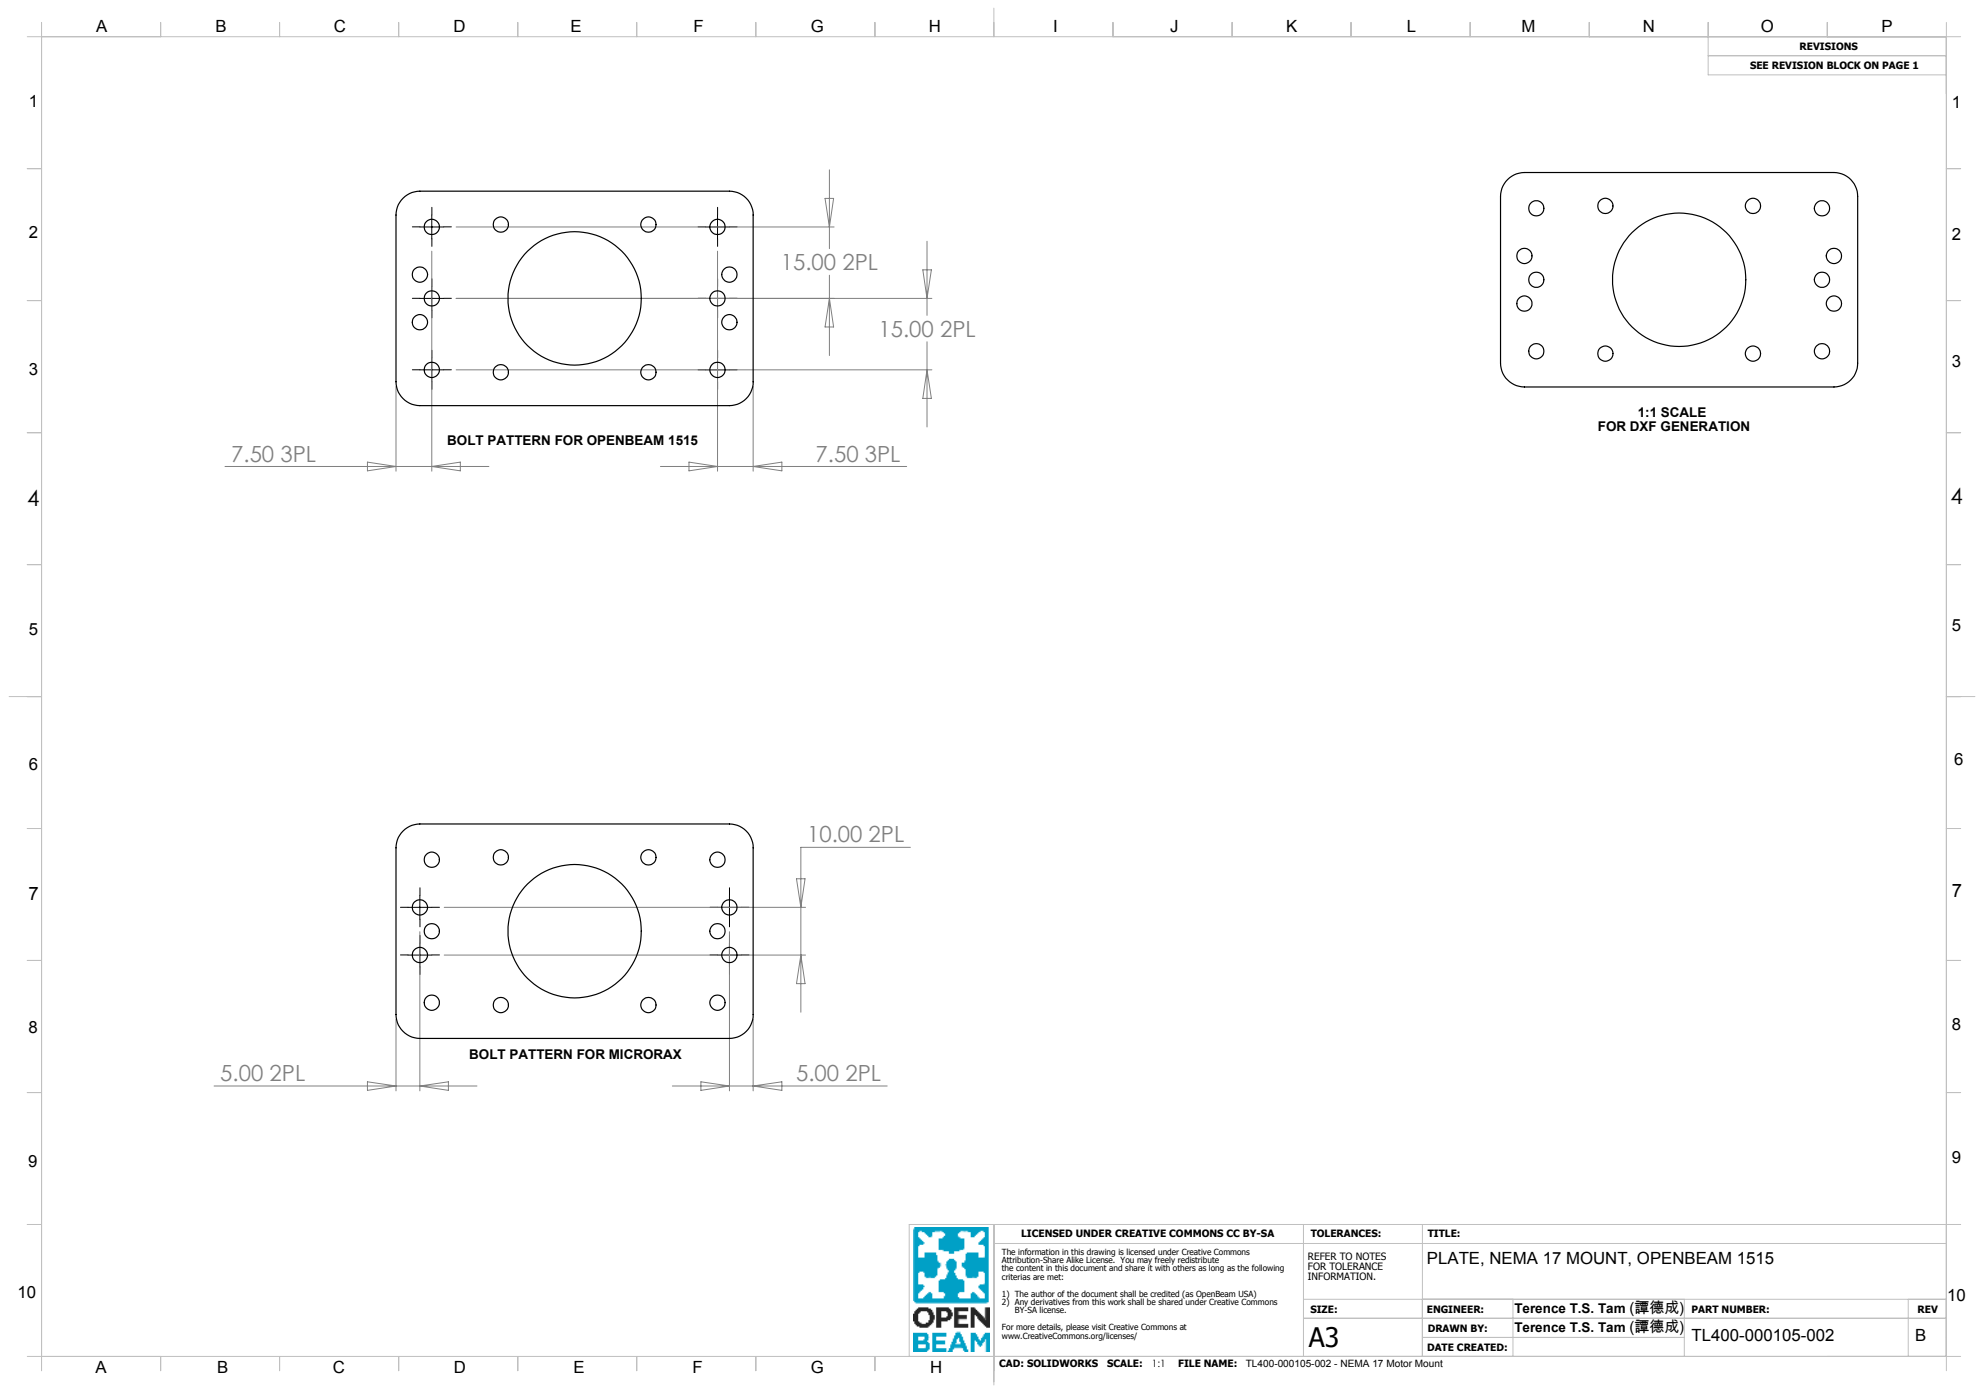
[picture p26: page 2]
CAD: SOLIDWORKS SCALE:; FILE NAME: 1:1; TL400-000105-002 DRAWN BY:; DATE CREATED:

SEE REVISION BLOCK ON PAGE 1

1:1 SCALE
FOR DXF GENERATION

BOLT PATTERN FOR OPENBEAM 1515

BOLT PATTERN FOR MICRORAX

LICENSED UNDER CREATIVE COMMONS CC BY-SA

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

REFER TO NOTES FOR TOLERANCE INFORMATION. | PLATE, NEMA 17 MOUNT, OPENBEAM 1515

SIZE: | ENGINEER: | Terence T.S. Tam (譚德成) | PART NUMBER: | REV

Terence T.S. Tam (譚德成)

TL400-000105-002 - NEMA 17 Motor Mount

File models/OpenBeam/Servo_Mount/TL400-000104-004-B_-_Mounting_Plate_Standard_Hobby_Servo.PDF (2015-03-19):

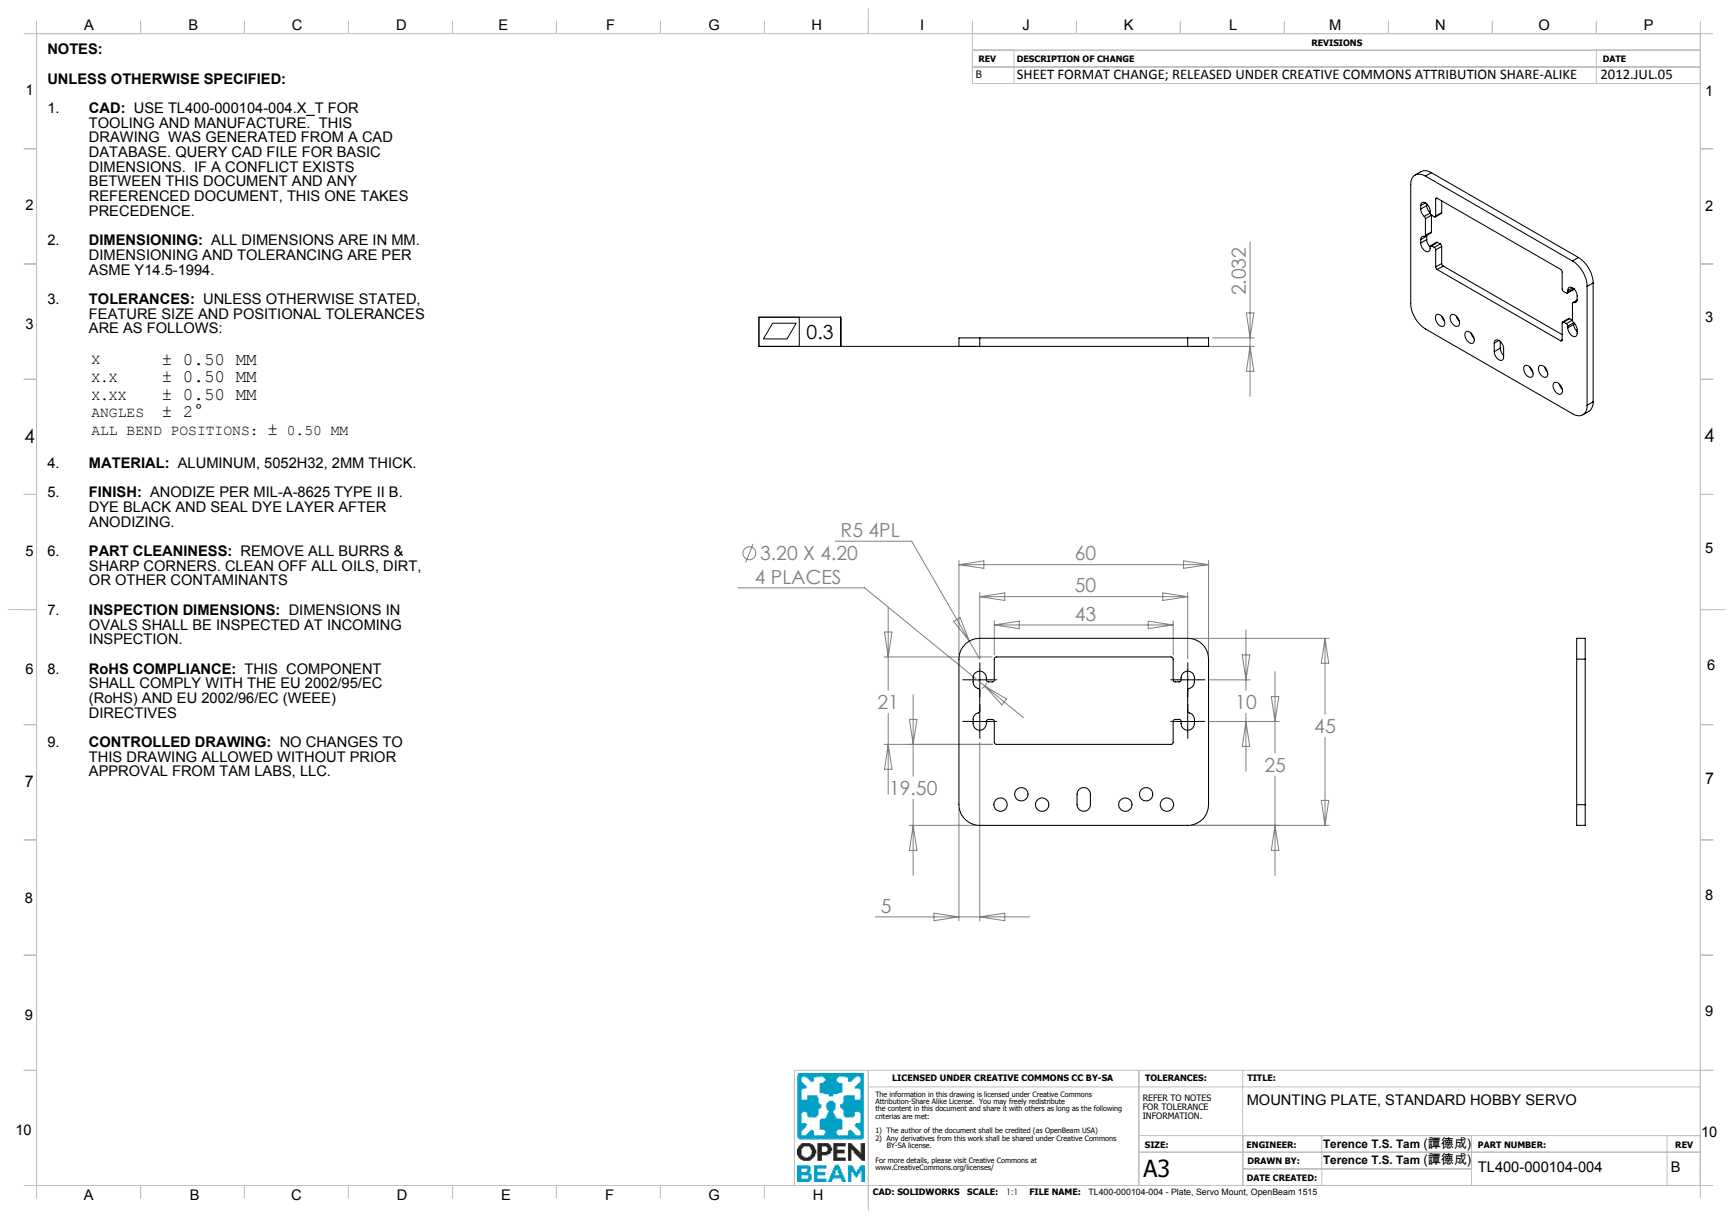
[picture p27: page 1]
4 PLACES; CAD: SOLIDWORKS SCALE:; FILE NAME: 1:1; TL400-000104-004 DRAWN BY:; DATE CREATED:

NOTES:
UNLESS OTHERWISE SPECIFIED:
1. CAD: USE TL400-000104-004.X_T FOR
TOOLING AND MANUFACTURE. THIS
DRAWING WAS GENERATED FROM A CAD
DATABASE. QUERY CAD FILE FOR BASIC
DIMENSIONS. IF A CONFLICT EXISTS
BETWEEN THIS DOCUMENT AND ANY
REFERENCED DOCUMENT, THIS ONE TAKES
PRECEDENCE.
2. DIMENSIONING: ALL DIMENSIONS ARE IN MM.
DIMENSIONING AND TOLERANCING ARE PER
ASME Y14.5-1994.
3. TOLERANCES: UNLESS OTHERWISE STATED,
FEATURE SIZE AND POSITIONAL TOLERANCES
ARE AS FOLLOWS:
ANGLES ± 2°
ALL BEND POSITIONS: ± 0.50 MM
4. MATERIAL: ALUMINUM, 5052H32, 2MM THICK.
5. FINISH: ANODIZE PER MIL-A-8625 TYPE II B.
DYE BLACK AND SEAL DYE LAYER AFTER
ANODIZING.
6. PART CLEANINESS: REMOVE ALL BURRS &

REV | DESCRIPTION OF CHANGE | DATE
B | SHEET FORMAT CHANGE; RELEASED UNDER CREATIVE COMMONS ATTRIBUTION SHARE-ALIKE | 2012.JUL.05

SHARP CORNERS. CLEAN OFF ALL OILS, DIRT,
OR OTHER CONTAMINANTS
7. INSPECTION DIMENSIONS: DIMENSIONS IN
OVALS SHALL BE INSPECTED AT INCOMING
INSPECTION.
8. RoHS COMPLIANCE: THIS COMPONENT

SHALL COMPLY WITH THE EU 2002/95/EC
(RoHS) AND EU 2002/96/EC (WEEE)
DIRECTIVES
9. CONTROLLED DRAWING: NO CHANGES TO
THIS DRAWING ALLOWED WITHOUT PRIOR
APPROVAL FROM TAM LABS, LLC.

LICENSED UNDER CREATIVE COMMONS CC BY-SA

The information in this drawing is licensed under Creative Commons
Attribution-Share Alike License. You may freely redistribute
the content in this document and share it with others as long as the following
criterias are met:
1) The author of the document shall be credited (as OpenBeam USA)
2) Any derivatives from this work shall be shared under Creative Commons
BY-SA license.
For more details, please visit Creative Commons at
www.CreativeCommons.org/licenses/

REFER TO NOTES FOR TOLERANCE INFORMATION. | MOUNTING PLATE, STANDARD HOBBY SERVO

SIZE: | ENGINEER: | Terence T.S. Tam (譚德成) | PART NUMBER: | REV

Terence T.S. Tam (譚德成)

TL400-000104-004 - Plate, Servo Mount, OpenBeam 1515

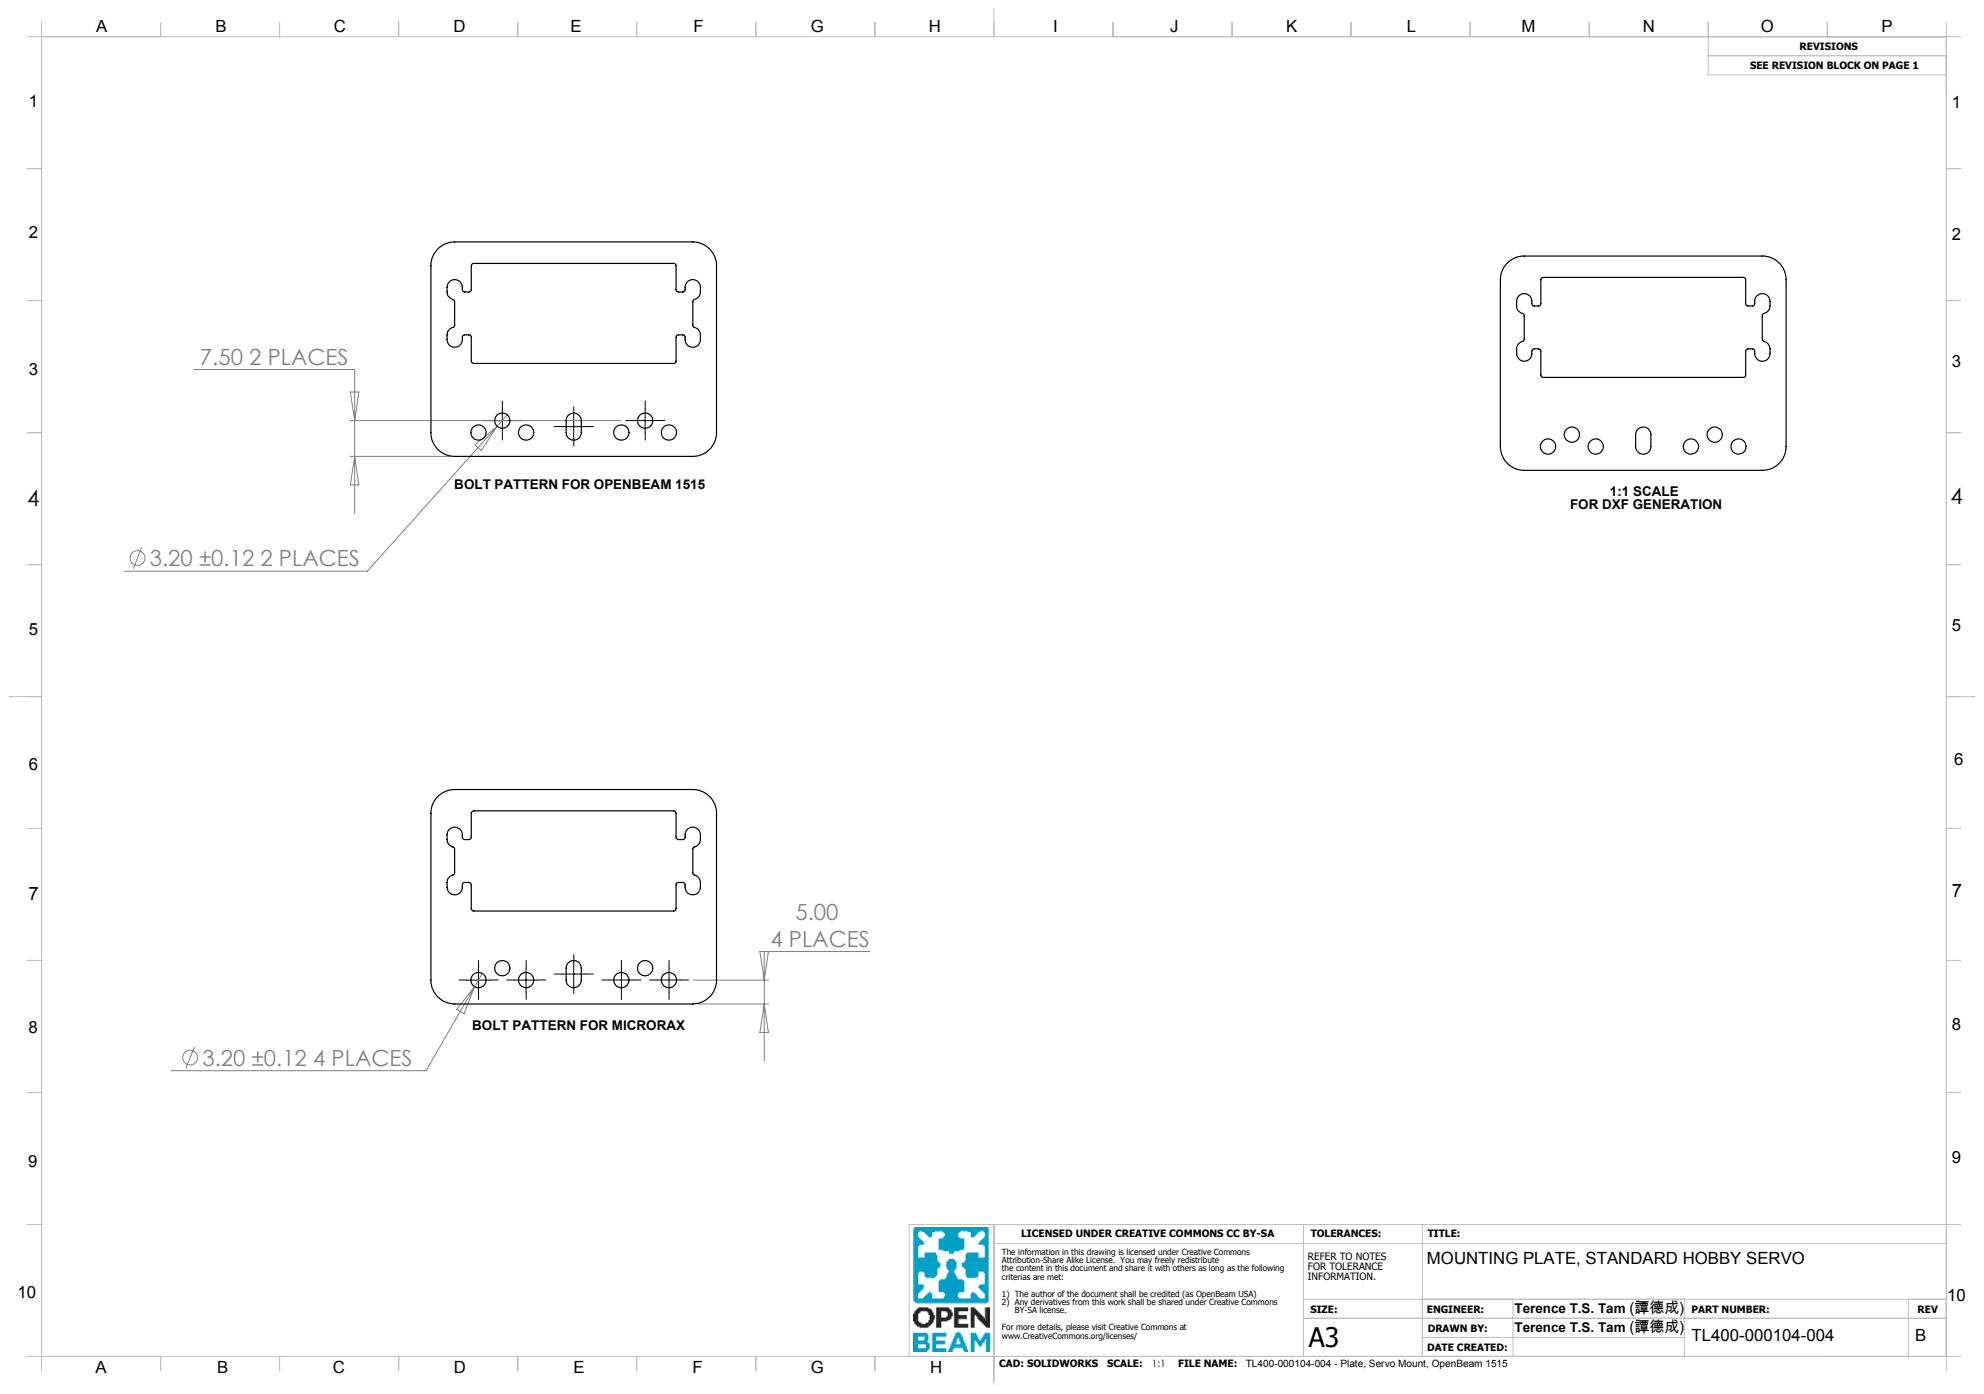
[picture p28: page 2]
4 PLACES; 3.20 ±0.12 4 PLACES; 7.50 2 PLACES; 3.20 ±0.12 2 PLACES; CAD: SOLIDWORKS SCALE:; FILE NAME: 1:1; TL400-000104-004 DRAWN BY:; DATE CREATED:

SEE REVISION BLOCK ON PAGE 1

BOLT PATTERN FOR OPENBEAM 1515

1:1 SCALE
FOR DXF GENERATION

BOLT PATTERN FOR MICRORAX

LICENSED UNDER CREATIVE COMMONS CC BY-SA

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

REFER TO NOTES FOR TOLERANCE INFORMATION. | MOUNTING PLATE, STANDARD HOBBY SERVO

SIZE: | ENGINEER: | Terence T.S. Tam (譚德成) | PART NUMBER: | REV

Terence T.S. Tam (譚德成)

TL400-000104-004 - Plate, Servo Mount, OpenBeam 1515

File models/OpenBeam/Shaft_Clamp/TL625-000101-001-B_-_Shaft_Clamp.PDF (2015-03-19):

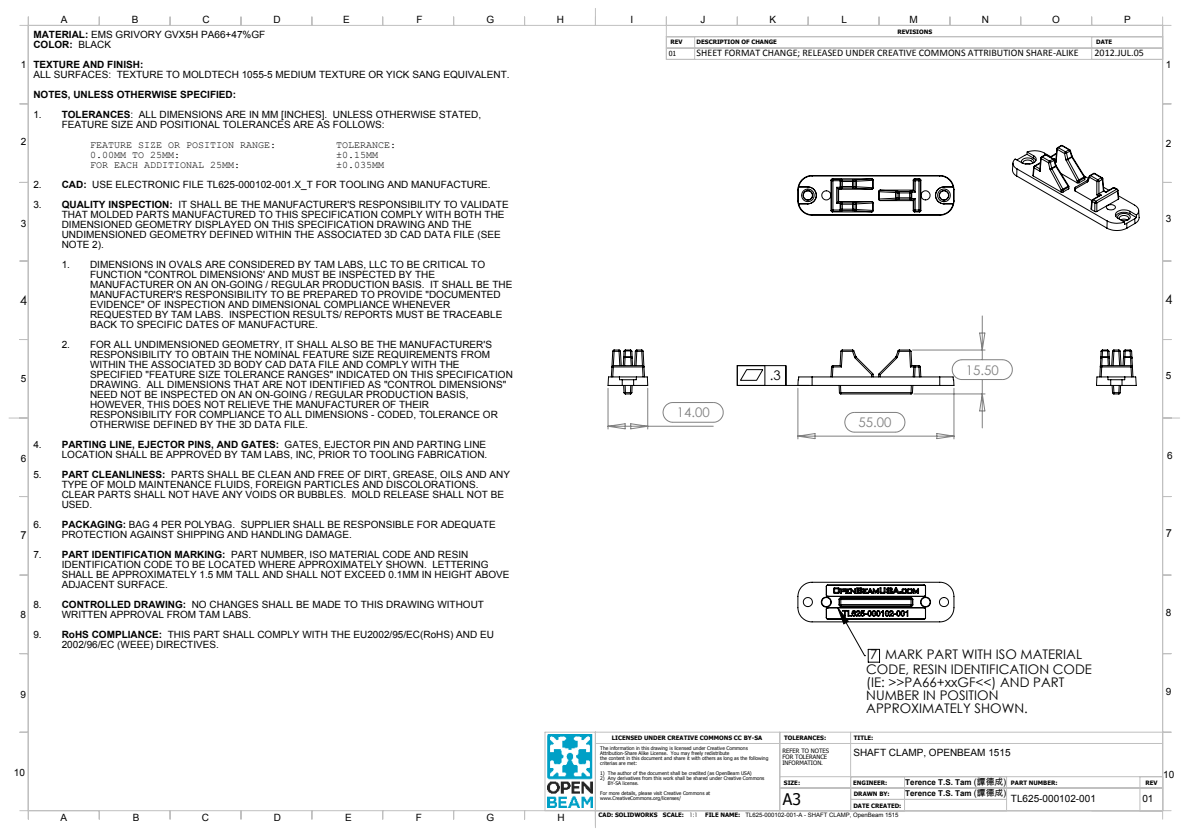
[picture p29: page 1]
FEATURE SIZE OR POSITION RANGE:; TOLERANCE:; FOR EACH ADDITIONAL 25MM:; CAD: SOLIDWORKS SCALE:; FILE NAME: 1:1; TL625-000102-001 DRAWN BY:; DATE CREATED:

MATERIAL: EMS GRIVORY GVX5H PA66+47%GF
COLOR: BLACK
TEXTURE AND FINISH:
ALL SURFACES: TEXTURE TO MOLDTECH 1055-5 MEDIUM TEXTURE OR YICK SANG EQUIVALENT.
NOTES, UNLESS OTHERWISE SPECIFIED:
1. TOLERANCES: ALL DIMENSIONS ARE IN MM [INCHES]. UNLESS OTHERWISE STATED,
FEATURE SIZE AND POSITIONAL TOLERANCES ARE AS FOLLOWS:

REV | DESCRIPTION OF CHANGE | DATE
01 | SHEET FORMAT CHANGE; RELEASED UNDER CREATIVE COMMONS ATTRIBUTION SHARE-ALIKE | 2012.JUL.05

2. CAD: USE ELECTRONIC FILE TL625-000102-001.X_T FOR TOOLING AND MANUFACTURE.
3. QUALITY INSPECTION: IT SHALL BE THE MANUFACTURER'S RESPONSIBILITY TO VALIDATE
THAT MOLDED PARTS MANUFACTURED TO THIS SPECIFICATION COMPLY WITH BOTH THE
DIMENSIONED GEOMETRY DISPLAYED ON THIS SPECIFICATION DRAWING AND THE
UNDIMENSIONED GEOMETRY DEFINED WITHIN THE ASSOCIATED 3D CAD DATA FILE (SEE
NOTE 2).
1. DIMENSIONS IN OVALS ARE CONSIDERED BY TAM LABS, LLC TO BE CRITICAL TO
FUNCTION "CONTROL DIMENSIONS' AND MUST BE INSPECTED BY THE
MANUFACTURER ON AN ON-GOING / REGULAR PRODUCTION BASIS. IT SHALL BE THE
MANUFACTURER'S RESPONSIBILITY TO BE PREPARED TO PROVIDE "DOCUMENTED
EVIDENCE" OF INSPECTION AND DIMENSIONAL COMPLIANCE WHENEVER
REQUESTED BY TAM LABS. INSPECTION RESULTS/ REPORTS MUST BE TRACEABLE
BACK TO SPECIFIC DATES OF MANUFACTURE.
2. FOR ALL UNDIMENSIONED GEOMETRY, IT SHALL ALSO BE THE MANUFACTURER'S
RESPONSIBILITY TO OBTAIN THE NOMINAL FEATURE SIZE REQUIREMENTS FROM
WITHIN THE ASSOCIATED 3D BODY CAD DATA FILE AND COMPLY WITH THE
SPECIFIED "FEATURE SIZE TOLERANCE RANGES" INDICATED ON THIS SPECIFICATION
DRAWING. ALL DIMENSIONS THAT ARE NOT IDENTIFIED AS "CONTROL DIMENSIONS"
NEED NOT BE INSPECTED ON AN ON-GOING / REGULAR PRODUCTION BASIS,
HOWEVER, THIS DOES NOT RELIEVE THE MANUFACTURER OF THEIR
RESPONSIBILITY FOR COMPLIANCE TO ALL DIMENSIONS - CODED, TOLERANCE OR
OTHERWISE DEFINED BY THE 3D DATA FILE.

4. PARTING LINE, EJECTOR PINS, AND GATES: GATES, EJECTOR PIN AND PARTING LINE
LOCATION SHALL BE APPROVED BY TAM LABS, INC, PRIOR TO TOOLING FABRICATION.
5. PART CLEANLINESS: PARTS SHALL BE CLEAN AND FREE OF DIRT, GREASE, OILS AND ANY
TYPE OF MOLD MAINTENANCE FLUIDS, FOREIGN PARTICLES AND DISCOLORATIONS.
CLEAR PARTS SHALL NOT HAVE ANY VOIDS OR BUBBLES. MOLD RELEASE SHALL NOT BE
USED.
6. PACKAGING: BAG 4 PER POLYBAG. SUPPLIER SHALL BE RESPONSIBLE FOR ADEQUATE
PROTECTION AGAINST SHIPPING AND HANDLING DAMAGE.
7. PART IDENTIFICATION MARKING: PART NUMBER, ISO MATERIAL CODE AND RESIN
IDENTIFICATION CODE TO BE LOCATED WHERE APPROXIMATELY SHOWN. LETTERING
SHALL BE APPROXIMATELY 1.5 MM TALL AND SHALL NOT EXCEED 0.1MM IN HEIGHT ABOVE
ADJACENT SURFACE.
8. CONTROLLED DRAWING: NO CHANGES SHALL BE MADE TO THIS DRAWING WITHOUT
WRITTEN APPROVAL FROM TAM LABS.
9. RoHS COMPLIANCE: THIS PART SHALL COMPLY WITH THE EU2002/95/EC(RoHS) AND EU
2002/96/EC (WEEE) DIRECTIVES.

7 MARK PART WITH ISO MATERIAL
CODE, RESIN IDENTIFICATION CODE
(IE: >>PA66+xxGF<<) AND PART
NUMBER IN POSITION
APPROXIMATELY SHOWN.

LICENSED UNDER CREATIVE COMMONS CC BY-SA

The information in this drawing is licensed under Creative Commons
Attribution-Share Alike License. You may freely redistribute
the content in this document and share it with others as long as the following
criterias are met:
1) The author of the document shall be credited (as OpenBeam USA)
2) Any derivatives from this work shall be shared under Creative Commons
BY-SA license.
For more details, please visit Creative Commons at
www.CreativeCommons.org/licenses/

REFER TO NOTES FOR TOLERANCE INFORMATION. | SHAFT CLAMP, OPENBEAM 1515

SIZE: | ENGINEER: | Terence T.S. Tam (譚德成) | PART NUMBER: | REV

01 Terence T.S. Tam (譚德成)

TL625-000102-001-A - SHAFT CLAMP, OpenBeam 1515

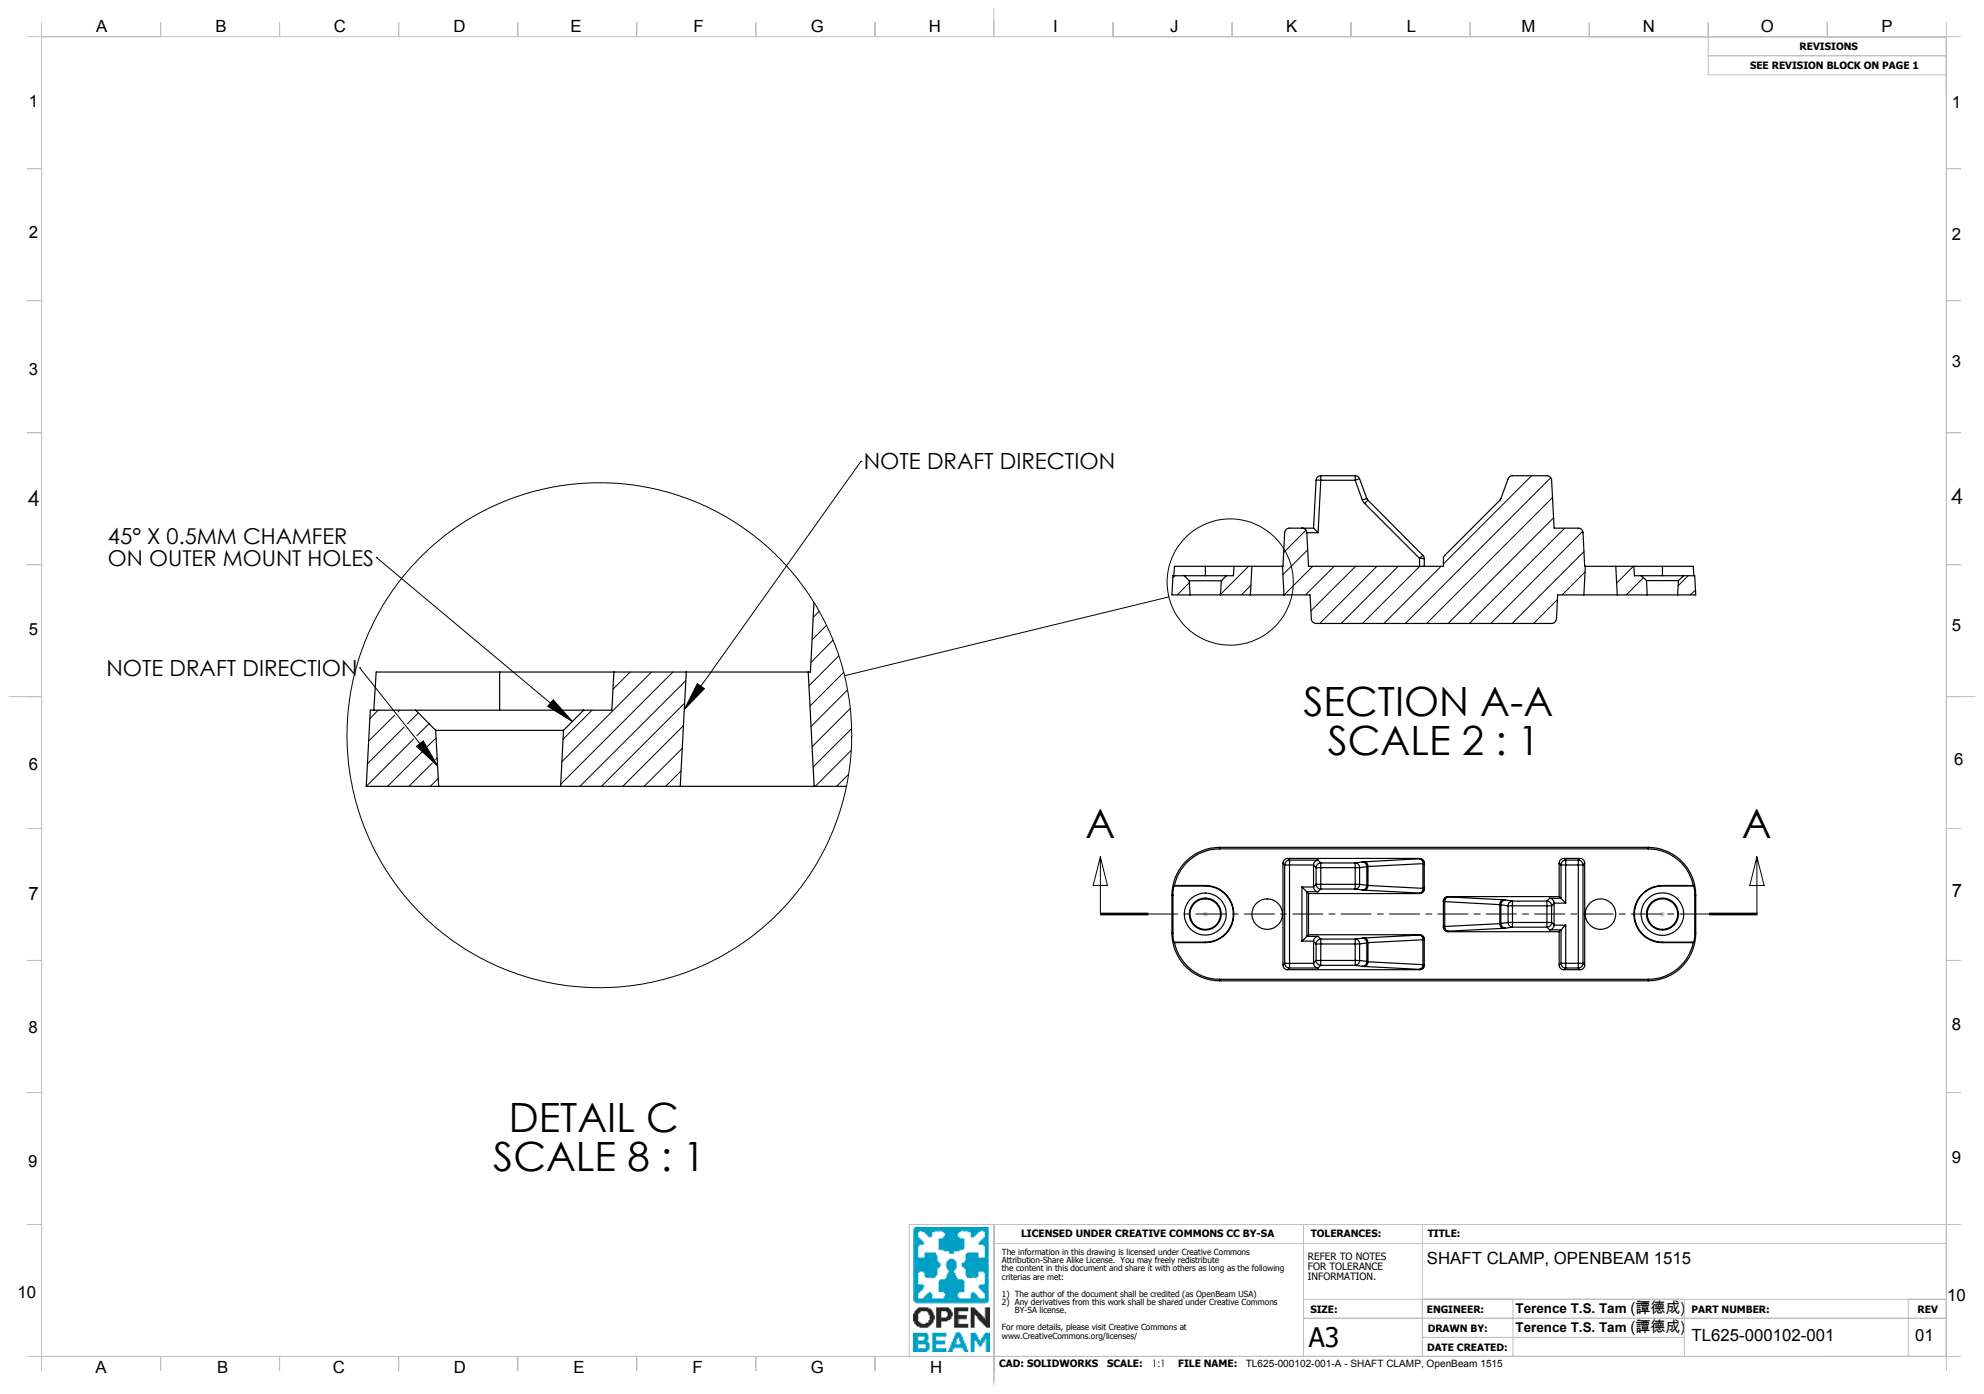
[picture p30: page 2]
SECTION A-A SCALE 2 : 1; DETAIL C SCALE 8 : 1; CAD: SOLIDWORKS SCALE:; FILE NAME: 1:1; TL625-000102-001 DRAWN BY:; DATE CREATED:

SEE REVISION BLOCK ON PAGE 1

NOTE DRAFT DIRECTION

45° X 0.5MM CHAMFER
ON OUTER MOUNT HOLES

LICENSED UNDER CREATIVE COMMONS CC BY-SA

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

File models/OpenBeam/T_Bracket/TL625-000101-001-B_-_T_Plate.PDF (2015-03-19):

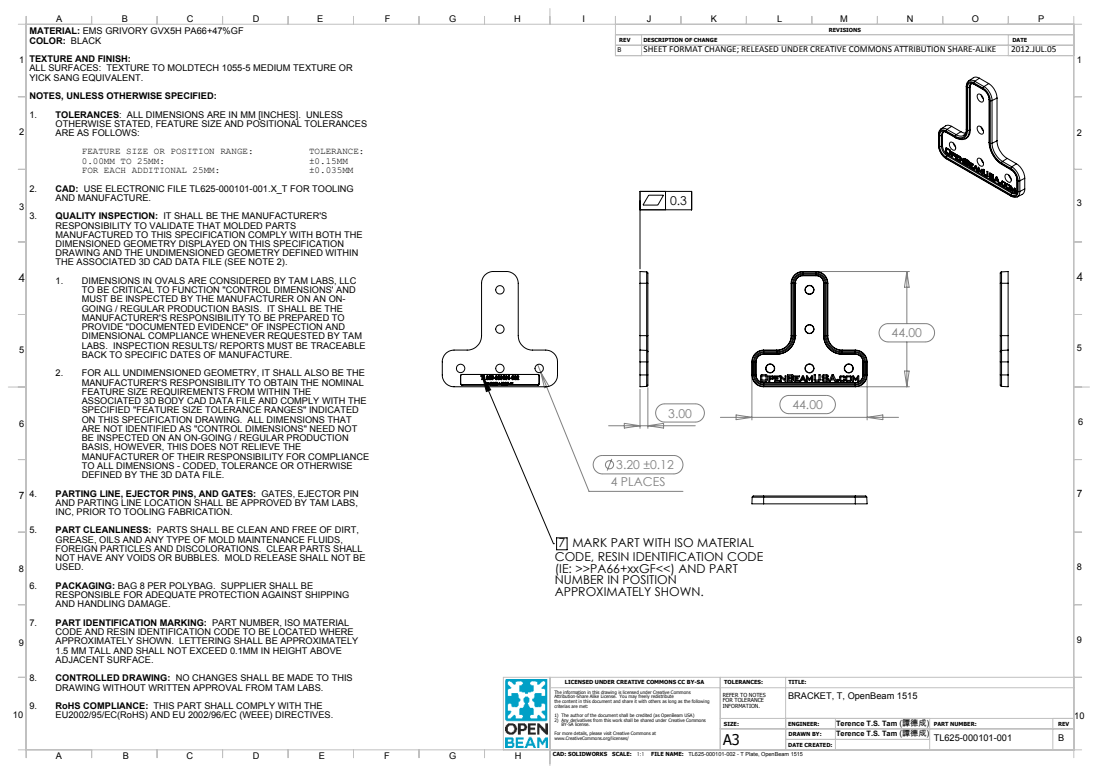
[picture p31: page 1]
3.20 ±0.12 4 PLACES; FEATURE SIZE OR POSITION RANGE:; TOLERANCE:; FOR EACH ADDITIONAL 25MM:; CAD: SOLIDWORKS SCALE:; FILE NAME: 1:1; TL625-000101-001 DRAWN BY:; DATE CREATED: TL625-000101-002 - T Plate, OpenBeam 1515

MATERIAL: EMS GRIVORY GVX5H PA66+47%GF
COLOR: BLACK
TEXTURE AND FINISH:
ALL SURFACES: TEXTURE TO MOLDTECH 1055-5 MEDIUM TEXTURE OR
YICK SANG EQUIVALENT.
NOTES, UNLESS OTHERWISE SPECIFIED:
1. TOLERANCES: ALL DIMENSIONS ARE IN MM [INCHES]. UNLESS
OTHERWISE STATED, FEATURE SIZE AND POSITIONAL TOLERANCES
ARE AS FOLLOWS:

REV | DESCRIPTION OF CHANGE | DATE
B | SHEET FORMAT CHANGE; RELEASED UNDER CREATIVE COMMONS ATTRIBUTION SHARE-ALIKE | 2012.JUL.05

2. CAD: USE ELECTRONIC FILE TL625-000101-001.X_T FOR TOOLING
AND MANUFACTURE.
3. QUALITY INSPECTION: IT SHALL BE THE MANUFACTURER'S
RESPONSIBILITY TO VALIDATE THAT MOLDED PARTS
MANUFACTURED TO THIS SPECIFICATION COMPLY WITH BOTH THE
DIMENSIONED GEOMETRY DISPLAYED ON THIS SPECIFICATION
DRAWING AND THE UNDIMENSIONED GEOMETRY DEFINED WITHIN
THE ASSOCIATED 3D CAD DATA FILE (SEE NOTE 2).
1. DIMENSIONS IN OVALS ARE CONSIDERED BY TAM LABS, LLC
TO BE CRITICAL TO FUNCTION "CONTROL DIMENSIONS' AND
MUST BE INSPECTED BY THE MANUFACTURER ON AN ON-
GOING / REGULAR PRODUCTION BASIS. IT SHALL BE THE
MANUFACTURER'S RESPONSIBILITY TO BE PREPARED TO
PROVIDE "DOCUMENTED EVIDENCE" OF INSPECTION AND
DIMENSIONAL COMPLIANCE WHENEVER REQUESTED BY TAM
LABS. INSPECTION RESULTS/ REPORTS MUST BE TRACEABLE
BACK TO SPECIFIC DATES OF MANUFACTURE.
2. FOR ALL UNDIMENSIONED GEOMETRY, IT SHALL ALSO BE THE
MANUFACTURER'S RESPONSIBILITY TO OBTAIN THE NOMINAL
FEATURE SIZE REQUIREMENTS FROM WITHIN THE
ASSOCIATED 3D BODY CAD DATA FILE AND COMPLY WITH THE
SPECIFIED "FEATURE SIZE TOLERANCE RANGES" INDICATED
ON THIS SPECIFICATION DRAWING. ALL DIMENSIONS THAT
ARE NOT IDENTIFIED AS "CONTROL DIMENSIONS" NEED NOT
BE INSPECTED ON AN ON-GOING / REGULAR PRODUCTION
BASIS, HOWEVER, THIS DOES NOT RELIEVE THE
MANUFACTURER OF THEIR RESPONSIBILITY FOR COMPLIANCE
TO ALL DIMENSIONS - CODED, TOLERANCE OR OTHERWISE
DEFINED BY THE 3D DATA FILE.

4. PARTING LINE, EJECTOR PINS, AND GATES: GATES, EJECTOR PIN
AND PARTING LINE LOCATION SHALL BE APPROVED BY TAM LABS,
INC, PRIOR TO TOOLING FABRICATION.
5. PART CLEANLINESS: PARTS SHALL BE CLEAN AND FREE OF DIRT,
GREASE, OILS AND ANY TYPE OF MOLD MAINTENANCE FLUIDS,
FOREIGN PARTICLES AND DISCOLORATIONS. CLEAR PARTS SHALL
NOT HAVE ANY VOIDS OR BUBBLES. MOLD RELEASE SHALL NOT BE
USED.
6. PACKAGING: BAG 8 PER POLYBAG. SUPPLIER SHALL BE
RESPONSIBLE FOR ADEQUATE PROTECTION AGAINST SHIPPING
AND HANDLING DAMAGE.
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

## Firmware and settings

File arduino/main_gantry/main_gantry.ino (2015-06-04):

/* 
 * This Arduino drives all of the motors on the turing machine using a motor shield.
 */

#include <Wire.h>
#include <Adafruit_MotorShield.h>
#include "utility/Adafruit_PWMServoDriver.h"
#include <Servo.h> 

#define MARKER_SERVO_DOWN       (112)
#define MARKER_SERVO_UP         (90)
#define ERASER_LIFT_SERVO_UP    (255)
#define ERASER_LIFT_SERVO_DOWN  (100)
#define ERASER_SPIN_SERVO_GO    (0)
#define ERASER_SPIN_SERVO_STOP  (255)

int potPin = 2;    // select the input pin for the potentiometer
int ledPin = 13;   // select the pin for the LED
int val = 0;       // variable to store the value coming from the sensor



// Create the motor shield object with the default I2C address
Adafruit_MotorShield AFMS = Adafruit_MotorShield(); 

// Connect a stepper motor with 200 steps per revolution (1.8 degree)
// to motor port #2 (M3 and M4)
Adafruit_StepperMotor *markerMotor = AFMS.getStepper(200, 2);
Adafruit_StepperMotor *tapeMotor = AFMS.getStepper(200, 1);

// We'll also test out the built in Arduino Servo library
Servo markerServo;
Servo eraserLiftServo;
Servo eraserSpinServo;

void setup() {
  Serial.begin(9600);
  
  AFMS.begin();  // create with the default frequency 1.6KHz
  //AFMS.begin(1000);  // OR with a different frequency, say 1KHz
  
  // Init our stepper that moves the marker
  markerMotor->setSpeed(1000);  // 10 rpm  
 
  // Init our stepper that feeds the tape 
  tapeMotor->setSpeed(10);
  
  // Attach a servo to pin #10
  markerServo.attach(10);
  eraserLiftServo.attach(9);
  eraserSpinServo.attach(11);
  
  eraserLift();
  eraserStop();
  markerLift();
  //gantryZero();
}



void markerLift() {
  markerServo.write(map(MARKER_SERVO_UP, 0, 255, 0, 180));
}

void markerLower() {
  markerServo.write(map(MARKER_SERVO_DOWN, 0, 255, 0, 180));
}

static uint16_t gantryPosition = 0;

void gantryZero(){
  gantryPosition = 0;
  markerMotor->step(3000, BACKWARD, SINGLE);
  markerMotor->step(1000, FORWARD, DOUBLE);
}

void gantryOut(){
  if(gantryPosition < 1600){
    gantryPosition += 1600;
    markerMotor->step(1600, FORWARD, DOUBLE);
  }
}

void gantryIn(){
  if(gantryPosition >= 1600){
    gantryPosition -= 1600;
    markerMotor->step(1600, BACKWARD, DOUBLE);
  }
}

void eraserLower(){
  eraserLiftServo.write(map(ERASER_LIFT_SERVO_DOWN, 0, 255, 0, 180));
}

void eraserLift(){
  eraserLiftServo.write(map(ERASER_LIFT_SERVO_UP, 0, 255, 0, 180));
}

void eraserSpin(){
  eraserSpinServo.write(map(ERASER_SPIN_SERVO_GO, 0, 255, 0, 180));
}

void eraserStop(){
  eraserSpinServo.write(map(ERASER_SPIN_SERVO_STOP, 0, 255, 0, 180));
}

void tapeMoveLeft() {
  tapeMotor->step(60, BACKWARD, DOUBLE);
}

void tapeMoveRight() {
  tapeMotor->step(60, FORWARD, DOUBLE);
}
void loop() {
  static uint8_t val = 128;
  uint8_t c;
  if(Serial.available()){
    c = Serial.read();
    
    switch(c){
    
      // Eraser functions
      case 'E':
        eraserLift();
        break;
      case 'e':
        eraserLower();
        break;
      case 'S':
        eraserSpin();
        break;
      case 's':
        eraserStop();
        break;
        
      // Marker functions
      case 'M':
        markerLift();
        break;
      case 'm':
        markerLower();
        break;
      case 'G':
        gantryOut();
        break;
      case 'g':
        gantryIn();
        break;
      case 'z':
        gantryZero();
        break;
      
      case '+':
        //markerLift();
        if(val < 252)
          val += 4;
        break;
      case '-':
        //markerLower();
        if(val > 3)
          val -= 4;
        break;
      
      ///
      //  Turing Machine Functions
      ///
       
      // Move tape Left
      case 'l':
        tapeMoveLeft();
        
        Serial.println("done");
        break;
      // Move tape Right
      case 'r':
        tapeMoveRight();
        
        Serial.println("done");
        break;
      
      // Write a 1
      case '1':
        markerLower();
        gantryOut();
        markerLift();
        gantryIn();
        
        Serial.println("done");
        break;
      // Write a 0
      case '0':
        markerLower();
        gantryOut();
        tapeMotor->step(20, FORWARD, DOUBLE);
        gantryIn();
        tapeMotor->step(20, BACKWARD, DOUBLE);
        markerLift();
        
        Serial.println("done");
        break;
        
      // Erase the current tape position
      case 'D':
        tapeMotor->step(125, FORWARD, DOUBLE);
        delay(100);
        eraserLower();
        delay(100);
        eraserSpin();
        delay(100);
        tapeMotor->step(30, BACKWARD, DOUBLE);
        delay(100);
        tapeMotor->step(30, FORWARD, DOUBLE);
        delay(100);
        tapeMotor->step(30, BACKWARD, DOUBLE);
        delay(100);
        tapeMotor->step(30, FORWARD, DOUBLE);
        delay(100);
        eraserStop();
        eraserLift();
        delay(100);
        tapeMotor->step(125, BACKWARD, DOUBLE);
        
        Serial.println("done");
        break;
        
      default:
        Serial.println("unknown");
        break;
    } // End switch
    
    
//    Serial.println(val);
//    eraserSpinServo.write(map(val, 0, 255, 0, 180));
  }
}

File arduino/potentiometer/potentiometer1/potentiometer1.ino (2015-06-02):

/* Potentiometer 1
 * This is the code for the left potentiometer to maintain tension on the film
 */

#include <Wire.h>
#include <Adafruit_MotorShield.h>
#include "utility/Adafruit_PWMServoDriver.h"

int potPin = 2;    // select the input pin for the potentiometer
int val = 0;       // variable to store the value coming from the sensor

// Create the motor shield object with the default I2C address
Adafruit_MotorShield AFMS = Adafruit_MotorShield(); 

// Connect a stepper motor with 200 steps per revolution (1.8 degree)
// to motor port #2 (M3 and M4)
Adafruit_StepperMotor *myMotor = AFMS.getStepper(200, 2);

void setup() {
  
  // Setup our serial
  Serial.begin(9600);
  while (!Serial) {
    ; // wait for serial port to connect. Needed for Leonardo only
  }
  
  AFMS.begin();  // create with the default frequency 1.6KHz
  
  myMotor->setSpeed(100);  // 100 rpm   
}

void loop() {
  
  // Read our potentiometer value
  val = analogRead(potPin);    // read the value from the sensor
  Serial.println(val);
  
  // Based on our thresholds, feed or draw in the film
  if (val > 360) {
    myMotor->step(1, FORWARD, DOUBLE); 
  } else if (val < 350) {
    myMotor->step(1, BACKWARD, DOUBLE); 
  }
}

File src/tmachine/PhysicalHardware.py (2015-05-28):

from AbstractHardware import *

import serial
import time

WRITE_ONE = "1"
WRITE_ZERO = "0"
ERASE = "D"
MOVE_LEFT = "l"
MOVE_RIGHT = "r"

class PhysicalHardware(AbstractHardware):
    """ Software-implemented Turing machine hardware

    Used for general testing of Turing machine logic and interface """

    def __init__(self, **kwargs):
        """ Creates the virtual hardware. 

        Keyword arguments:
         + tape_length = 1000    <- Length of tape in units
         + init        = []      <- starting data of tape (calls initialize)
         """

        self.__serial = serial.Serial(kwargs["serial_name"], 9600, timeout=1)
        time.sleep(2)
            
        self.__tape_length = 1000
        if "tape_length" in kwargs.keys():
            self.__tape_length = kwargs["tape_length"]

        self.__tape = [None] * self.__tape_length

        self.__position = self.__tape_length / 2 # int division

        if "init" in kwargs.keys():
            self.initialize(kwargs["init"])

    def _send_command(self, command):
        
        print "*** Sending command (%s) to Arduino..."%command
        self.__serial.write(command)
        self.__serial.write("\n")
        self.__serial.flush()
        
        rtn = self.__serial.readline()
        rtn = rtn.strip()
        
        while rtn != "done\r\n":
            rtn = self.__serial.readline()
            continue

        return True
    
    def moveLeft(self):
        """ moves the tape x units to the left """
        newPos = self.__position + 1
        if newPos >= self.__tape_length:
            raise Exception("Out of (Virtual) Tape!")
        else:
            self._send_command(MOVE_LEFT)
            self.__position = newPos

    def moveRight(self):
        """ moves the tape x units to the left """
        newPos = self.__position - 1
        if newPos < 0:
            raise Exception("Out of (Virtual) Tape!")
        else:
            self._send_command(MOVE_RIGHT)
            self.__position = newPos
    
    def write(self,value):
        """ Writes value to current position in tape"""
        
        if value != self.__tape[self.__position]:
            self.__tape[self.__position] = value
            
            # Erase whatever is already there
            if self.__tape[self.__position] != None:
                self._send_command(ERASE)

            # Write our new value
            if value == "1":
                self._send_command(WRITE_ONE)
            elif value == "0":
                self._send_command(WRITE_ZERO)
            elif value == None:
                print "* Write None. Doing nothing."
            else:
                print "*** ERROR: Got a write value that we don't support: %s"%value
    
    def read(self):
        """ Reads the value in the current position"""
        return self.__tape[self.__position]


    def erase(self):
        """ Erase the value on the tape in the current position. """
        self.__tape[self.__position] = None
    
        # Only erase if we have to
        if self.__tape[self.__position] != None:
            self._send_command(ERASE)
        
    
    def initialize(self,tape):
        """ Initializes starting data for the tape"""
        for i in range(len(tape)):
            self.__tape[self.__position + i] = tape[i]
    
            # Clean our tape
            self._send_command(ERASE)
            
            # Write our initial value
            if tape[i] == "1":
                self._send_command(WRITE_ONE)
            elif tape[i] == "0":
                self._send_command(WRITE_ZERO)
            
            # Move left
            self._send_command(MOVE_LEFT)

        # Move our write head back
        for i in range(len(tape)):
            self._send_command(MOVE_RIGHT)
    
    def bulk_erase(self):
        """ Deletes everything on the tape """
        self.tape = [None] * self.__tape_length

    def tape(self):
        """ For debug use only: prints and returns the whole tape"""
        return self.__tape

    def position(self):
        """ For debug use only: prints and returns the current location of the tape """
        return self.__position

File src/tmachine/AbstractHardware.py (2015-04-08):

from abc import ABCMeta, abstractmethod

class AbstractHardware:
	""" An abstract class that all hardware interfaces are derived from. 

	Descended classes will be a VirtualHardWare and Hardware, 
	allowing for software testing and real implementation to use
	the same interface. 

	Methods:

	-- moveLeft(units)
	-- moveRight(units)
	-- write(symbol)
	-- read
	-- initialize(array[symbol])
	-- bulk_erase
	"""

	__metaclass__ = ABCMeta

	@abstractmethod
	def moveLeft(self,x):
		""" moves the tape x units to the left """
		pass

	@abstractmethod
	def moveRight(self,x):
		""" moves the tape x units to the right """
		pass

	@abstractmethod
	def write(self,value):
		""" Writes value to current position in tape"""
		pass

	@abstractmethod
	def erase(self):
		""" Erase current position on the tape """
		pass

	@abstractmethod
	def read(self):
		""" Reads the value in the current position"""
		pass

	@abstractmethod
	def initialize(self,tape):
		""" Initializes starting data for the tape"""
		pass

	@abstractmethod
	def bulk_erase(self):
		""" Deletes everything on the tape """
		pass

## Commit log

2015-02-03 Adding powerpoint version to get the ball rolling. Will return to this after lunch.
2015-02-03 powerpoint update
2015-03-18 Fixing Jacks bugs for him.
    [VirtualHardware.py]
2015-03-18 Fixing some bugs with tape init function.
    [VirtualHardware.py]
2015-03-19 Initial test of uplaoding models. Includes OpenBeam models as well as the initial design for the spool holder.
    [Adafruit_Rod_Support.SLDPRT, Angle_Connector.SLDPRT, Assembly_Spool.SLDASM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]
2015-03-30 Addition of new model elements.
    [Adafruit_Guide_Carriage.SLDPRT, Adafruit_Guide_Rail.SLDPRT, Adafruit_Guide_Rail_Cut.SLDPRT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]
2015-03-31 Purchase request
    Initial set of additional parts required for the MkI design.
    [Purchase_20150330_AdditionalParts.xlsx]
2015-04-03 Upaded parts order to add LEDs, Markers, and Camera cable, also updated our .gitignore
    [Purchase_20150330_AdditionalParts.xlsx, parts_order_04_03_2015.xlsx]
2015-04-23 Model Update
    Current working revision of the Turing Machine mechanical model.
    [Assembly_Film_Drive.SLDASM, Assembly_Film_Feeder.SLDASM, Assembly_Gantry_Superstructure.SLDASM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]
2015-04-23 Dimension changes
    Modified spool crossmember length for angle brackets and adjusted the
    wooden base.
    [Assembly_Spool_Holder.SLDASM, Beam_Spool_Support_Crossmember.SLDPRT, Display_Base.SLDPRT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]
2015-04-24 Adding parts to be 3d printed.
    [Spool_Hub.STL, Timing_Pulley.STL, gantry_marker_clamp.STL]
2015-04-27 Adding teeth to film sproket and also adding 2 parts to be 3d printed.
    [Film_Sprocket.SLDPRT, Film_Sprocket.STL, Plate_NEMA_Modified.STL]
2015-04-29 updated hole in sprocket to be 8mm
    [Film_Sprocket.SLDPRT, Film_Sprocket.STL]
2015-05-06 Added STL for pot coat hanger mount
2015-05-14 Adding arduino code.
2015-05-15 Updating film sproket
    [Film_Sprocket.SLDPRT, Film_Sprocket.STL]
2015-05-22 Updating some items to be laser cut.
    [Carriage_Mounting_Plate.DWG, Potentiometer_Holder.DWG, Potentiometer_Holder.SLDPRT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]
2015-05-22 Updated potentiometer
    [Potentiometer_Holder.DWG]
2015-05-22 Adding plate to move servo to the back of the main gantry.
    [Plate_NEMA_Modified2.DWG, Plate_NEMA_Modified2.SLDPRT]
2015-05-23 More parts to laser cut.
    [Lift_Arm.DWG, Lift_Arm_Driven.DWG]
2015-05-23 Added larger version of mounting plate so we could drill it out.
    [Carriage_Mounting_Plate.DWG]
2015-05-27 Adding the sketch for our main gantry.
2015-05-27 Updated arduino code to return a done code.
2015-05-27 Added actual turing program that does unary addition and interacts with the arduino over the serial port.
2015-05-28 Adding binary addition and some bug fixes. (L and R may be flipped in the binary adder)
    [PhysicalHardware.py]
2015-06-02 Cleaning up repo
    [Carriage_Mounting_Plate.DWG, Carriage_Mounting_Plate_Larger.DWG, Film_Sprocket.STL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]
